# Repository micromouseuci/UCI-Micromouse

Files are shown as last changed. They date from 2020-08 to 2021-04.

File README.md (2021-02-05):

# UCI Micromouse

This is the official GitHub of Micromouse @ UCI. This repository is here to allow you to build your own mouse for competition. 

#### Club Resources
 * [__Official Club Website__](https://micromouseuci.github.io/) - Get updates on club meetings and club information
 * [__Micromouse @UCI Team Drive__](https://drive.google.com/drive/folders/1fHwfOaCsH3-F_LZoAcfiGgn9cWiebsPj) - Reference Sheets, Lecture Slides, and more informative documents
 * [__YouTube Playlist__](https://www.youtube.com/playlist?list=PLTnmBeaLzeHIIcfAZqYvjoWuxOcVnpV9Z) - Official Micromouse@UCI playlist that includes helpful video references on a wide range of subjects, ranging from soldering and safety to PID control and ChibiOS
 * [__Facebook__](https://www.facebook.com/groups/153805515376853) - Club Facebook (only UCI students can join)
 
 #### Navigation
 To help you navigate through this repository, here is an overview of each section.
 1. <strong>Schematic Reference</strong> - Shows the schematic of the PCB. Use this to refer back to the PCB as you are soldering and testing components on the PCB. 
 2. <strong>Setting Up Arduino and Teensy</strong> - How to download and set up the Arduino software and Teensy drivers
 3. <strong>Soldering Components</strong> - simple instructions on how to solder each component onto the PCB.
 4. <strong>Testing</strong> - testing components using breadboards
 5. <strong>Software</strong> - programming instructions and suggestions

 <details>
 <summary><strong>Schematic Reference</strong></summary>
 <p>This is the schematic for Micromouse at UCI's PCB. The parts are listed below the image, with the labels in parentheses. Below the labels are further explanations of each circuit so that you can get an understanding of how each circuit works and why we included them in the PCB</p>
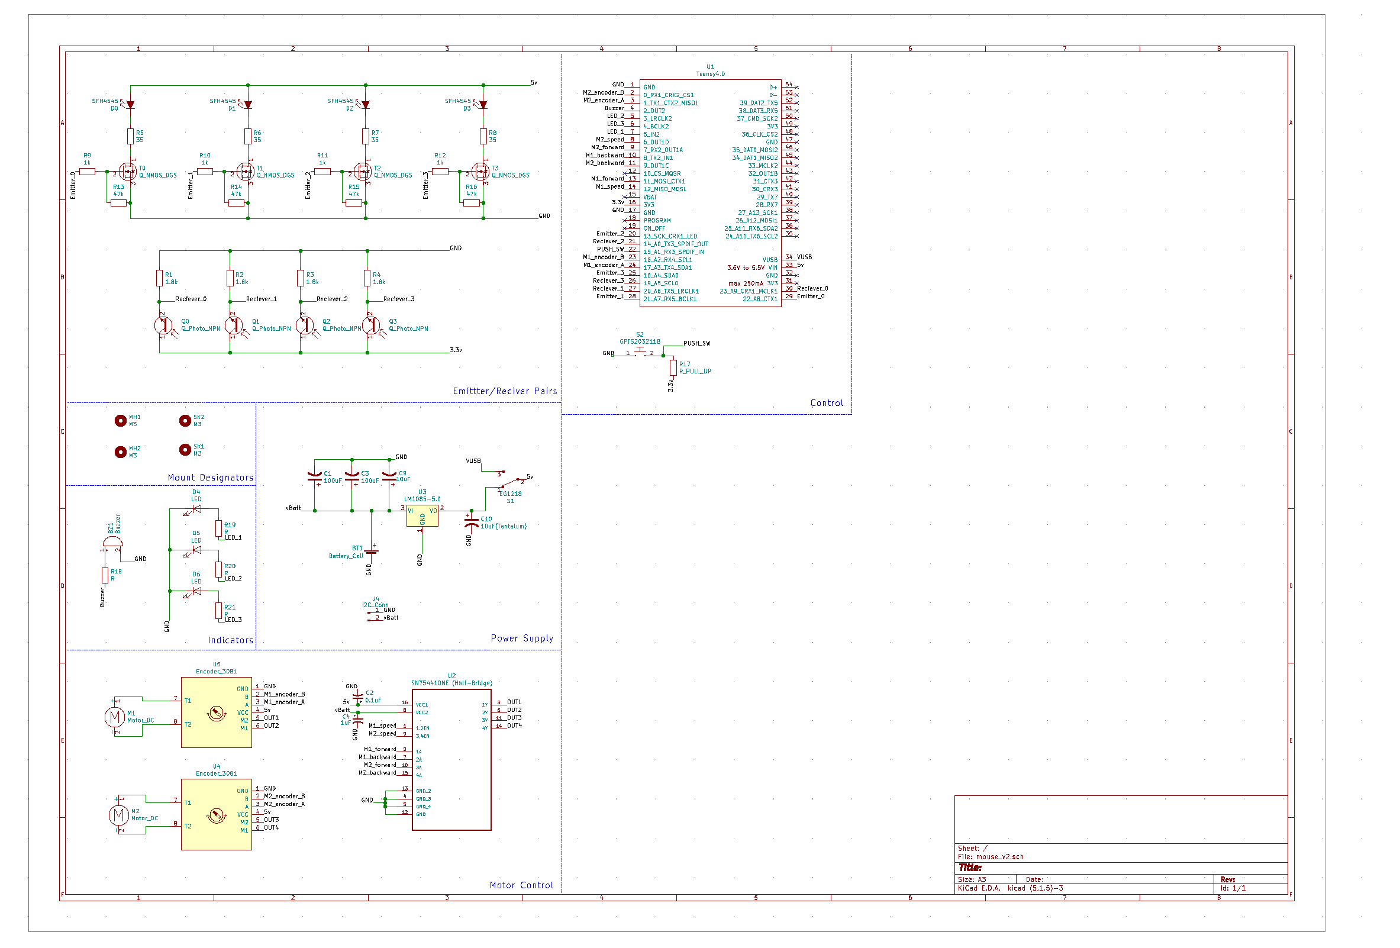
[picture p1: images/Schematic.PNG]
 
 
* [__SN754410NE__](https://www.digikey.com/product-detail/en/texas-instruments/SN754410NE/296-9911-5-ND/380180) _(U2)_ - Motor driver, used to control the speed and direction of the two motors.
* [__Teensy 3.2__](https://www.pjrc.com/teensy/teensy31.html) _(U1)_- Processor, will run code.
* [__IR Emitters__]() _(D0-D3)_ - Send an IR signal, which will bounce off walls, allowing for the reciever to read. Each is connected to a digital pin on the Teensy, allowing them to individual turn on and off.
* [__IR Reciever__]() _(Q0-Q3)_ - Reads how strong the IR signal is, depending on the value it reads it is able to detect if there is a wall, and how may cells away it is.
* [__Pololu 3081__](https://www.pololu.com/product/3081) _(U5, U4)_ - Motor encoders, used to keep track of wheel rotations.
* [__LM1085 (3A)__](http://www.ti.com/product/LM1085) _(U3)_ - Voltage regulator, a LDO regulator that gives a 5V source from the LiPo. 3A version.
* [__Switch__](http://www.google.com/search?q=mechanical+keyboard+switch) _(SW1)_ - Any mechanical keyboard switch
* [__Buzzer__](https://www.amazon.com/BETAFPV-Terminals-Electronic-Continuous-12X9-5mm/dp/B073RH8TQK) _(BZ1)_ - ~5mm buzzer pin spacing, the small ones in the link fit.
* [__LEDs__](http://www.google.com/search?q=3528+smd+led) _(D4, D5)_ - Any 3528 sized led rated for at least 3.3v
* [__Voltage Regulator (Linear)__](https://www.digikey.com/product-detail/en/stmicroelectronics/LD1085V50/497-3436-5-ND/669220) - Used to step voltage down
* __1.8KΩ__ _(R1, R2, R3, R4)_ - Current limiting resistors for Receivers.
* __35Ω__ _(R5, R6, R7, R8)_ - Current limiting resistor for Recievers.
* __47kΩ__ _(R13, R14, R15, R16)_ - Pull Up resistor for switch. Value based on the LED bought. [Calculate](http://www.ohmslawcalculator.com/led-resistor-calculator)
* __1kΩ__ _(R9, R10, R11, R12)_ - Resistors for MOSFET gate

 <details>
 <summary><strong>Emitter/Receiver Pair Circuit</strong></summary>
 </details>
 
 <details>
 <summary><strong>Power Supply Circuit</strong></summary>
 </details>

 <details>
 <summary><strong>Motor Control Circuit</strong></summary>
 </details>

 <details>
 <summary><strong>Indicator Circuit</strong></summary>
 </details>

 </details>
 
 <details>
 <summary><strong>Setting Up Arduino and Teensy</strong></summary>
 
 <p>In order to run your scripts on your computer, you will need to install Arduino.</p>
 
 * [__Download Arduino Software__]( https://www.arduino.cc/en/software) - Download the correct version based on the system you are using. Avoid downloading the Zip file if you are using Windows.
 * [__Download Teensyduino__](https://www.pjrc.com/teensy/td_download.html) - Download the Teensyduino software for your system. Make sure that you select the Teensyduino, as there are many links on this website that point to the Arduino website that you had downloaded the Arduino software from.

 </details>

<details>
 <summary><strong>Soldering Components</strong></summary>
 
 <p>The components must be soldered in order to maintain a solid electrical connection between two circuit elements. For ease, it's recommended that you follow the order listed below of components to solder. This will help prevent a mess or short circuits.</p>

   <ul><details>
 <summary><strong>Capacitors</strong></summary>
  </details></ul>

 <ul><details><summary><strong>IR Emitters and Receivers</strong></summary>
  <br> <li>On the schematic, the IR Emitters are labeled as D0, D1, D2, and D3. Find the corresponding labels on the PCB. They should be at the front of the board</li>
  <li>Place the shorter end of the emitter in the positive throughole of the corresponding pad and the longer end through the negative side. For reference, the D0 pad is shown below.</li>
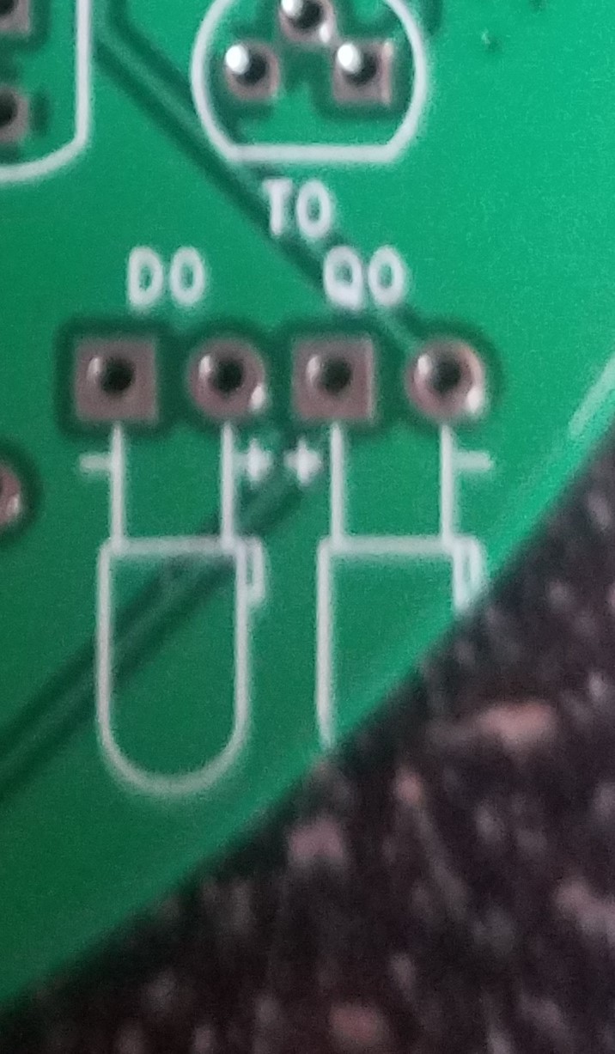
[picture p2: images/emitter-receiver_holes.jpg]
  
  <li>After inserting the emitter all the way, bend the emitter's leads so that the emitter lines up parallel to the PCB AND it is centered on the emitter sillhouette on the PCB. You can now solder the emitter. </li>
  <li>Repeat the same process for the IR Receivers. The receivers are located right next to the emitters, and are labelled as Q0, Q1, Q2, and Q3. For the receivers, the short end is also the positive end</li>
  <li>When you're soldering the components, make sure that the LEDs line up with the sillhouettes as much as possible. In other words, the length of the leads above the PCB should be as short as possible. This will ensure that one receiver from one set will not have interference from an emitter of another set. </li>
  </details></ul>
 
 <ul><details><summary><strong>Motors and Encoders</strong></summary>
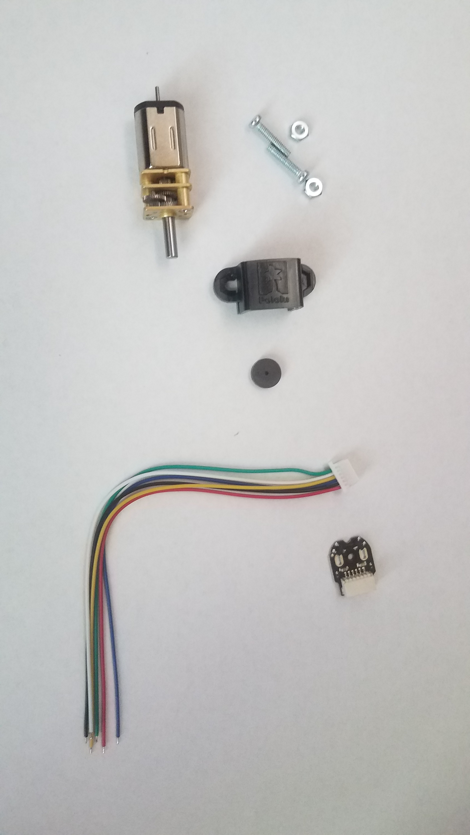
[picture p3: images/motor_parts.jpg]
 
 <ul>The image above shows all the components you will need to install your motor to your PCB.</ul>
 <ul>The first step is to attach the JST connector (the wires) to the encoder. The encoder is the mini black circuit board with a connecter pin for the JST.</ul>
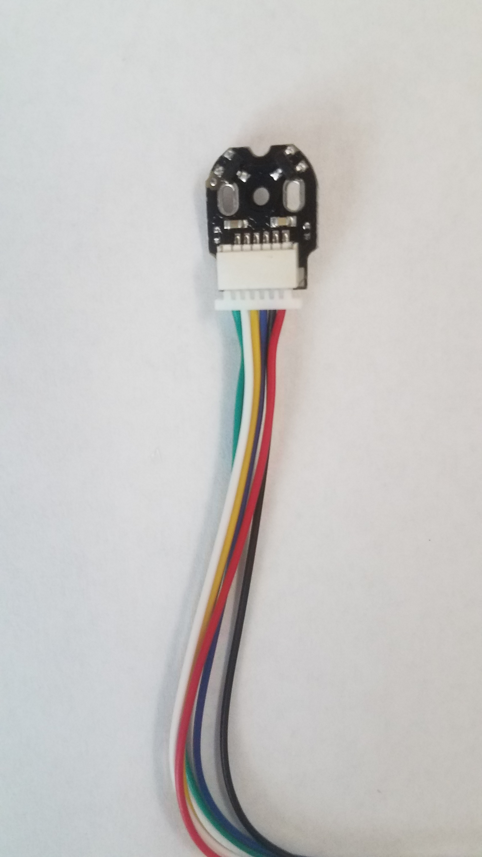
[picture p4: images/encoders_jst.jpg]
 
 <ul>To solder the encoder to the motor, use the image below as a reference. Make sure the encoder is perfectly parallel to the back end of the motor; if the encoder is crooked, it may cause some additional problems. Cover those holes on the encoder with solder while also making sure that the motor pins are touching the solder. This way, the motor pins are electrically connected to the encoders through solder. Give a slight tug to the encoder to make sure that it is firmly attached to the motor and is not loose. If it is loose, re-solder the encoder until it fits perfectly.</ul>
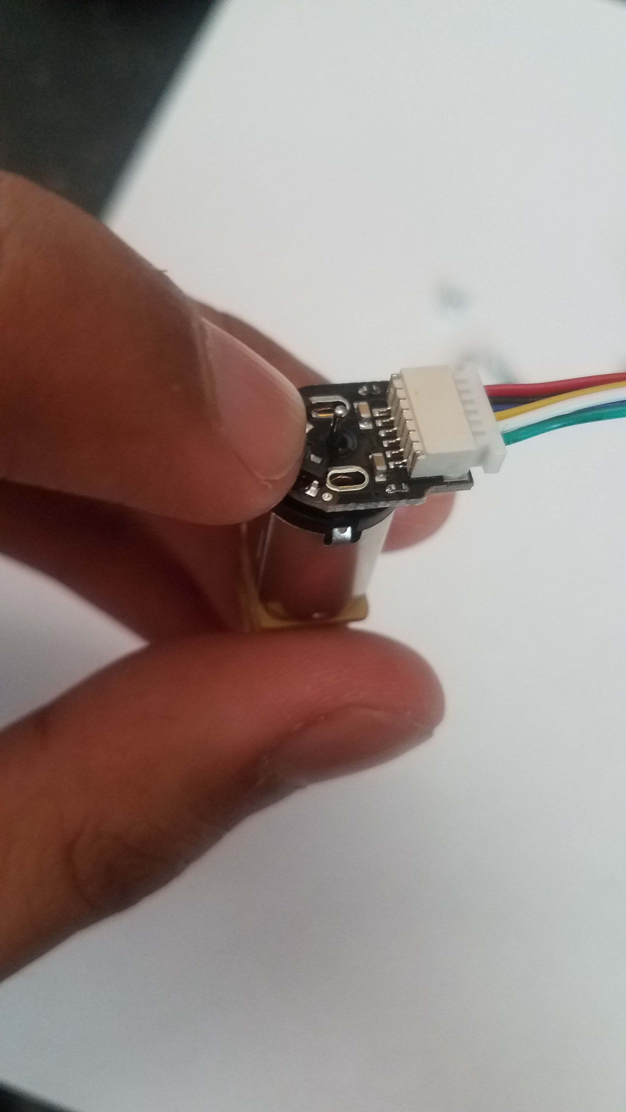
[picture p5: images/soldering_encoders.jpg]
 
 <ul>Finally, attach the magnet to the motor by inserting it through the mini shaft. The final product should look like the image below.  </ul>
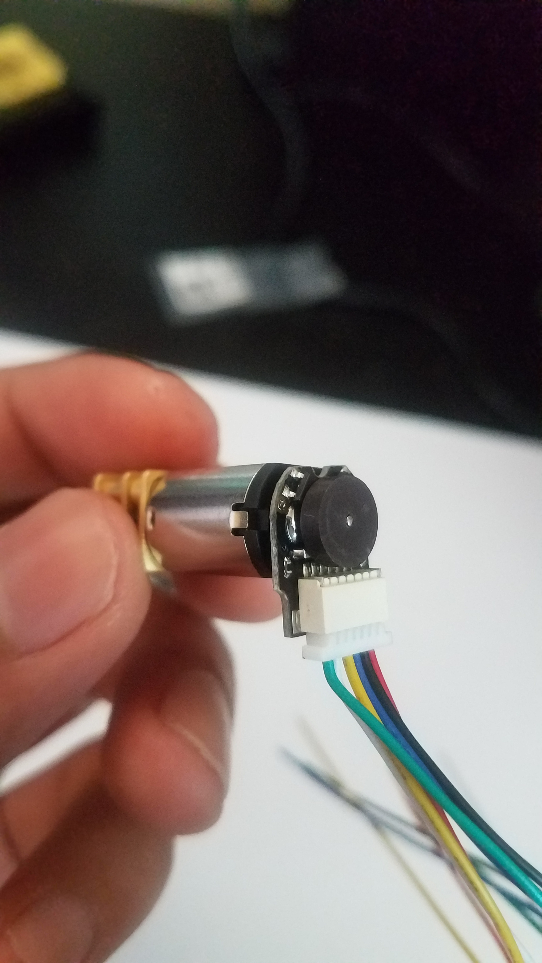
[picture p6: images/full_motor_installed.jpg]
 
 <ul> When it comes time to install the motor onto the PCB, you will need to make sure to have your motor offsets ready. First, place the motor offset onto the PCB, lining up with the motor holes. </ul>
 </details></ul>
 
 <ul><details>
 <summary><strong>MOSFETs and Resistors</strong></summary>
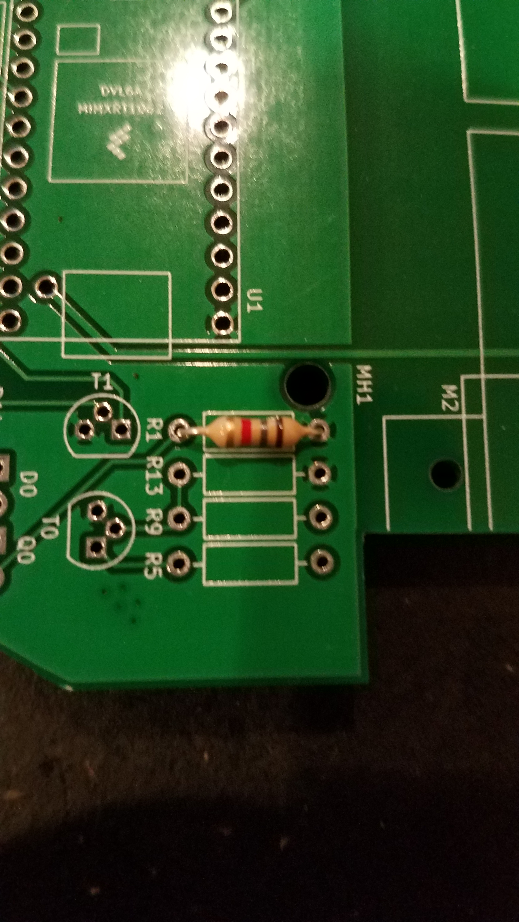
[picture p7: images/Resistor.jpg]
  
 <p>To solder the resistor, first make sure that the right resistor value is selected. Choosing the incorrect resistor value may result in irregular functionality; to determine which resistor must be used, first look at the KiCAD schematic of the mouse. Each resistor on the PCB is labeled as "R#" (i.e. R7). Find the corresponding resistor value on the schematic, and that will be the resistor value needed at that point (i.e. R7 is labeled as 35 ohms, so you will need a 35 ohm resistor at R7). To solder, simply bend the resistor and insert them into the holes specified (as shown above). The ceramic part of the resistor should be lined up with the rectangular engraving on the PCB and should touch the PCB. Solder the ends of the resistor at the bottom of the PCB, and then cut off the ends. The final product should look like this:</p>
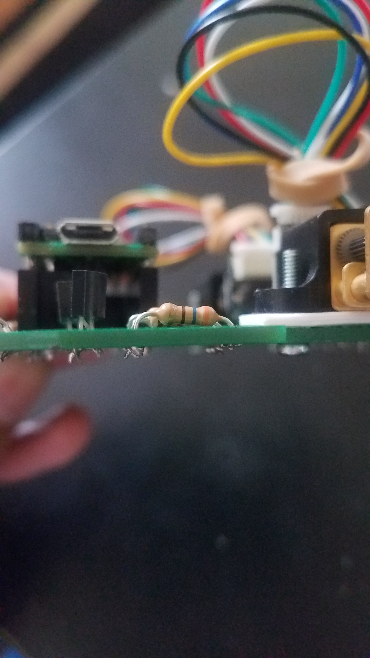
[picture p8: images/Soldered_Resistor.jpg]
 
 
 <p>The MOSFETs will be soldered on in a similar manner. All the MOSFET pads will be labeled as "T#" (i.e. T2) on the board. Place the MOSFET on the pad, with the flat face lined up with the straight edge of the MOSFET sillhouette. This will ensure the correct orientation of the transistor. Push the MOSFET in as much as you can. Solder the leads from the bottom of the board and cut off the ends. </p>
 
  </details></ul>

 <ul><details>
 <summary><strong>Voltage Regulator</strong></summary>
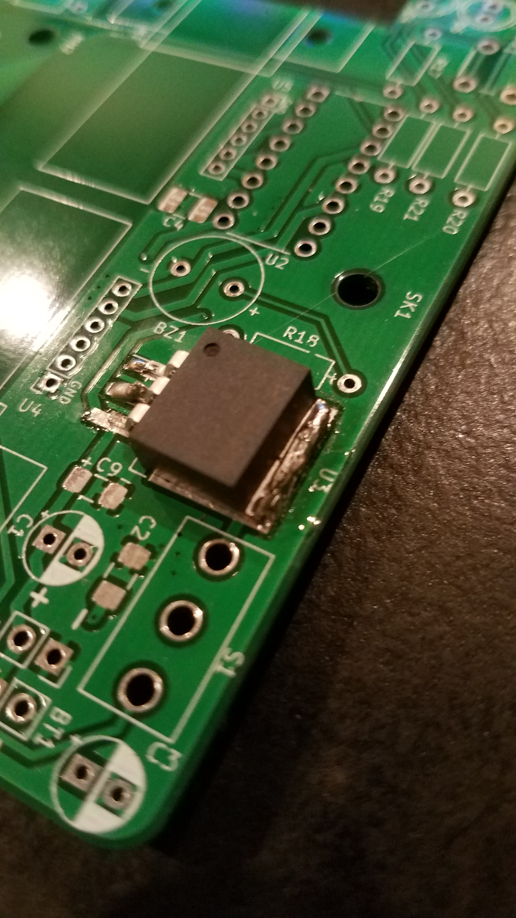
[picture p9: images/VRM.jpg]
 
 <p>YouTube Video (https://youtu.be/L_DIpklxXcI).</p>
  </details></ul> 

   <ul><details>
 <summary><strong>Switches and Buzzer</strong></summary>
  </details></ul>
  
   <ul><details>
 <summary><strong>Header Pins & Dip Socket</strong></summary>
 <ul>The header pins and dip socket are used for easy replacement of the Teensy and motor driver respectively in the event that they burn out. </ul>
 <ul>For the Teensy, you will need two 1x14 headers and one 1x5 header. Solder them on individually in the location shown below</ul>
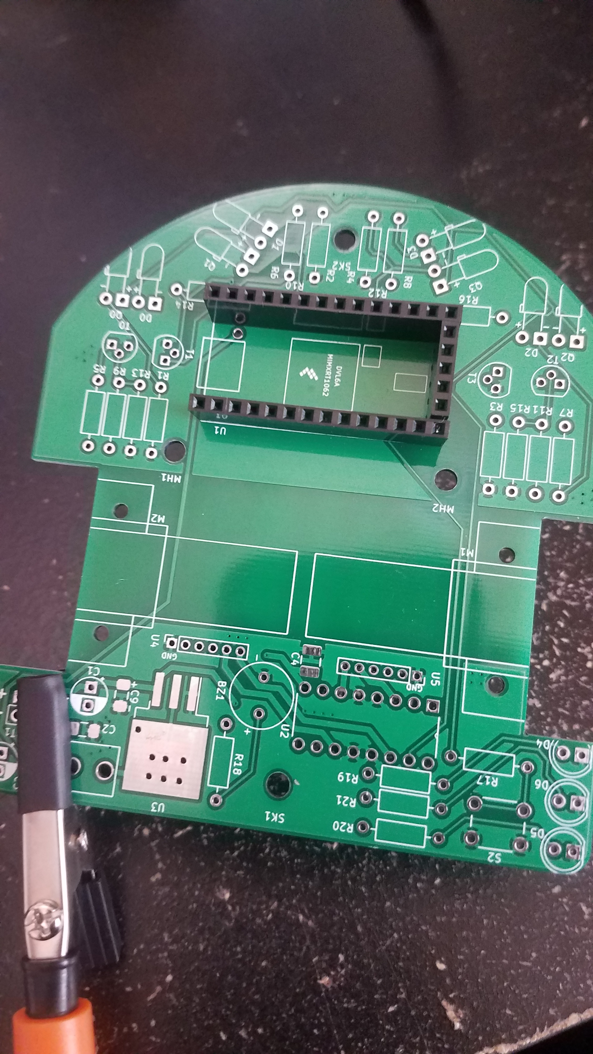
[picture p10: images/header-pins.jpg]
 
  
  </details></ul>
  <ul><details>
  <summary><strong>Header Pins for Teensy</strong></summary>
 <p>To add connections to the Teensy, male header pins must be installed onto the Teensy. Open the pack of male header pins, and break off two pieces of 14-unit pins (since the Teensy has 14 pins lengthwise) and one 5-unit piece (widthwise). When soldering the pins on, ensure that the black caps go UNDER the Teensy board, and not on top (image shown below). Once you solder them, cut off the top leads. You will also need to insert 1 pin into the final hole in the Teensy. You should now be able to place the Teensy on the header pins.  </p>
 
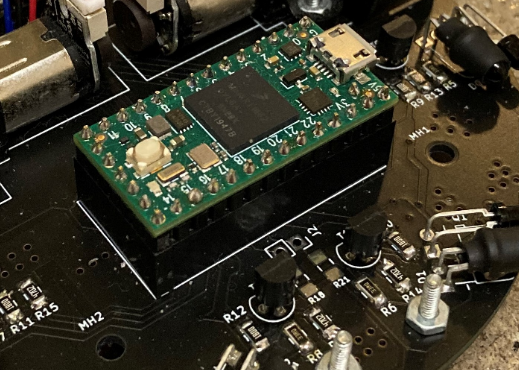
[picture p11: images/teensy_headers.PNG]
 
 
  </details></ul>
 
</details>
 
<details>
<summary><strong>Testing</strong></summary>
 
 <ul><details><summary><strong>IR Sensors</strong></summary>

</details></ul>

<ul><details>
<summary><strong>Motors</strong></summary>

</details></ul>

</details>
 
<details>
<summary><strong>Software</strong></summary>

#### Interrupts

* Interrupts are needed to keep track of the wheels revolution. When the wheels position changes, the motor encoder will send a signal to the Teensy. A total of 12 signals will be sent per 1 revolution. Interrupts allow it so the Teensy can update values as soon as the encoder sends the signal (asynchronously). If the encoders were updated in the main loop theres a good chance for some signals to be missed, causing the revolution count to be inaccurate.   

* To add an interrupt run the [attatchInterrupt](https://www.arduino.cc/reference/en/language/functions/external-interrupts/attachinterrupt/) function in setup. Syntax is **attatchInterrupt(pin, func, mode)**. The second parameter specifies the function that gets executed when the interrupt is triggered. In our case we want to put in a function that will add to the count of an encoder variable. The third parameter specifies what will trigger the interrupt. For example "CHANGE" will make the interrupt trigger whenever the pin changes value, however, "FALLING" will make the interrupt trigger only when the pin goes from HIGH to LOW. Read link for more info.

#### Variables

* tickCount - Two variables, one for each motor. When interrupt its triggered, increment the tick count by 1.
* emitterState - One for each emitter. Stores the current state of the emitter

#### Functions

* readReciever() - One method for each reciever. Returns the value read by reciever
* setEmitterState(x) - One method for each emitter. Set the state of the emitter to on or off.
* getSwitchState() - Return the value of the switch
* runMotorTime(m, speed, sec) - Set specific motor at speed for given amount of seconds. Uses delay function to count time.
* runMotorRev(m, speed, rev) - Runs a specific motor at speed for given amount of revolutions. Uses the encoder varible to count revolutions.
* setLED(l, brightness) - Sets a specific led to a certian brightness.
* setBuzzer(strength) - Sets the buzzer to a given strength.

#### More Functions
* turnRight() - Use encoders and tickCounts of both motors to make a percise right turn
* turnLeft() - similar to turnRight()
* goForward() - Use encoders to go straight.
* turnAround() - turnRight * 2

 </details>
 
 <details>
<summary><strong>3D Printed Parts</strong></summary>
 </details>

### Other Resources

<li><a href="https://git-scm.com/book/en/v2" target="_blank"><strong>Git Markdown</strong></a></li>
<li><a href="https://www.sparkfun.com/tutorials/223" target="_blank"><strong>How to Read a Datasheet</strong></a></li>

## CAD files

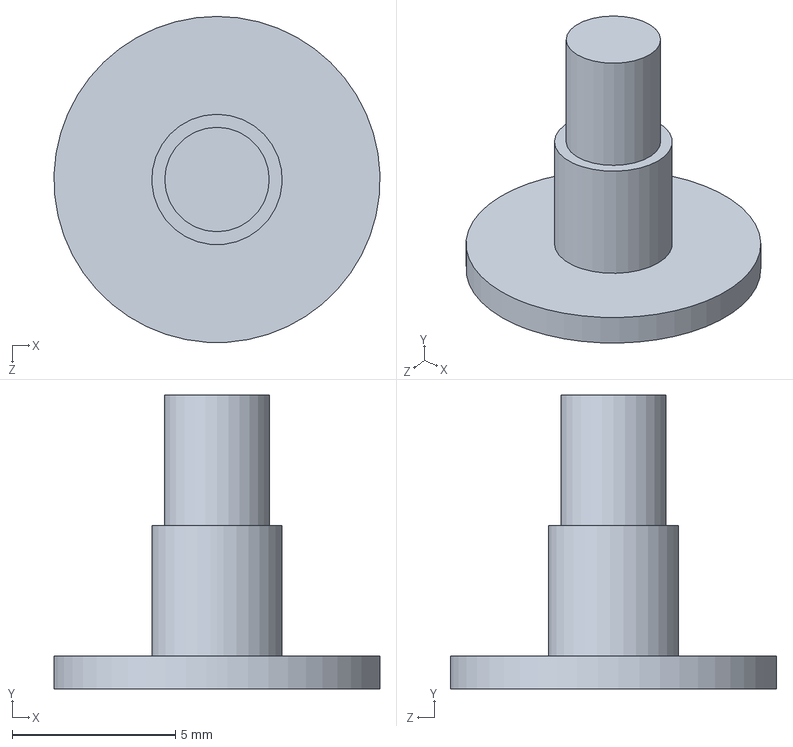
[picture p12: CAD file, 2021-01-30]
CAD Files/flat skates.SLDPRT
9.99 x 9.00 x 10.0 mm

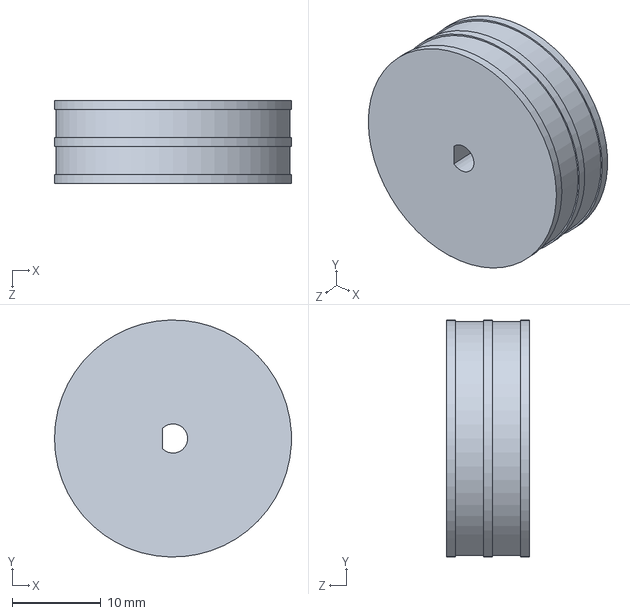
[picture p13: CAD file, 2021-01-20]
CAD Files/27 Rubber Band Wheel.SLDPRT
26.8 x 26.7 x 9.35 mm

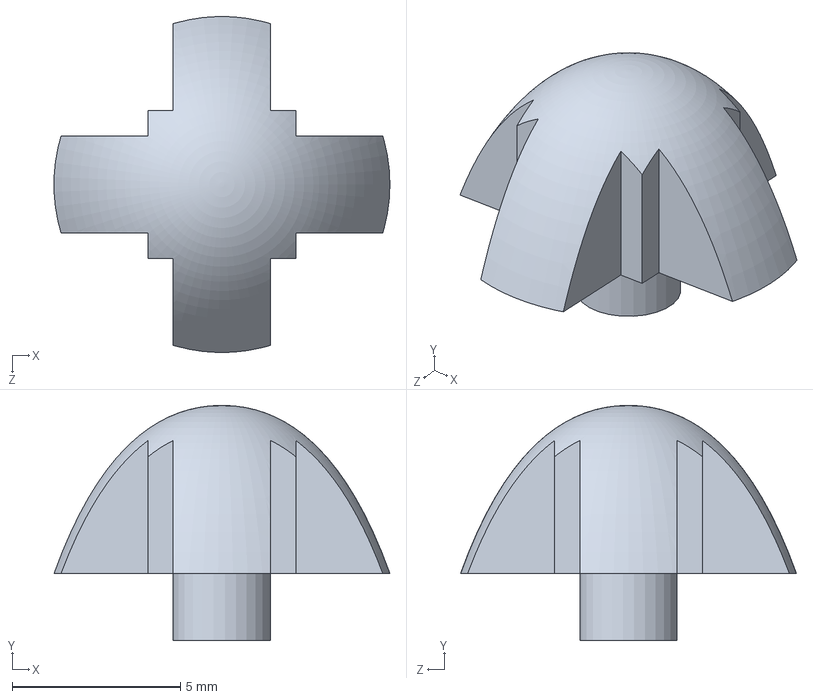
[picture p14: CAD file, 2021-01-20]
CAD Files/Mouse Skates.SLDPRT
10.00 x 7.00 x 10.00 mm

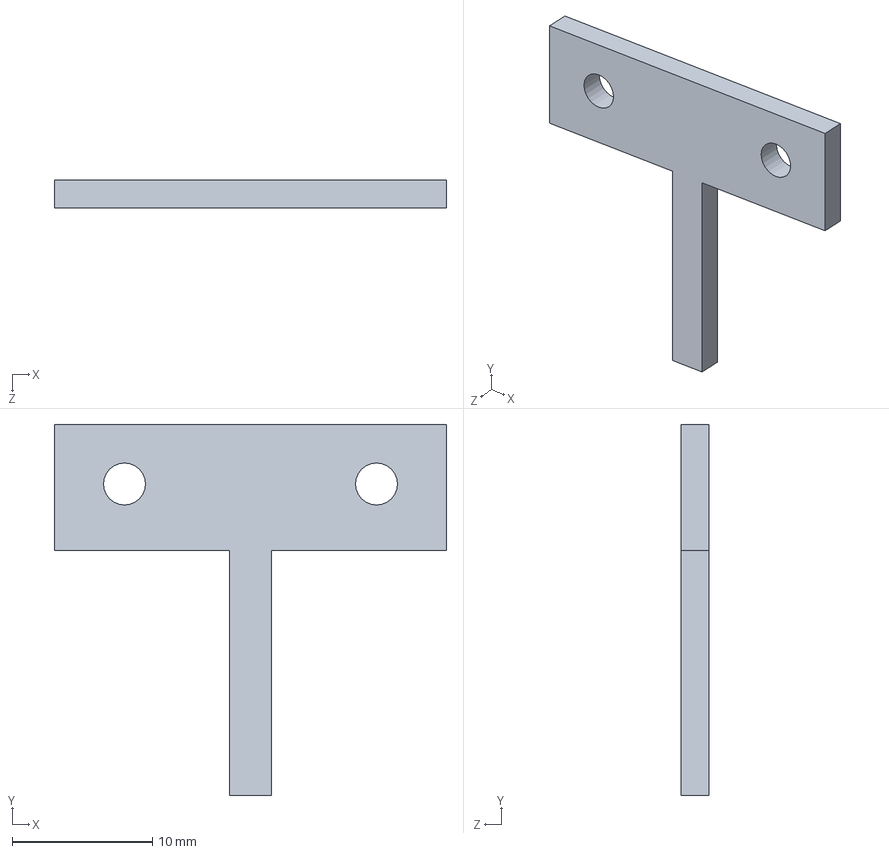
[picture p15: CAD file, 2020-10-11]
CAD Files/Motor Offset.SLDPRT
28.0 x 26.5 x 2.00 mm

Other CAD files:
CAD Files/27 Rubber Band Wheel.STL
CAD Files/Mouse Skates.STL
CAD Files/flat skates.STL

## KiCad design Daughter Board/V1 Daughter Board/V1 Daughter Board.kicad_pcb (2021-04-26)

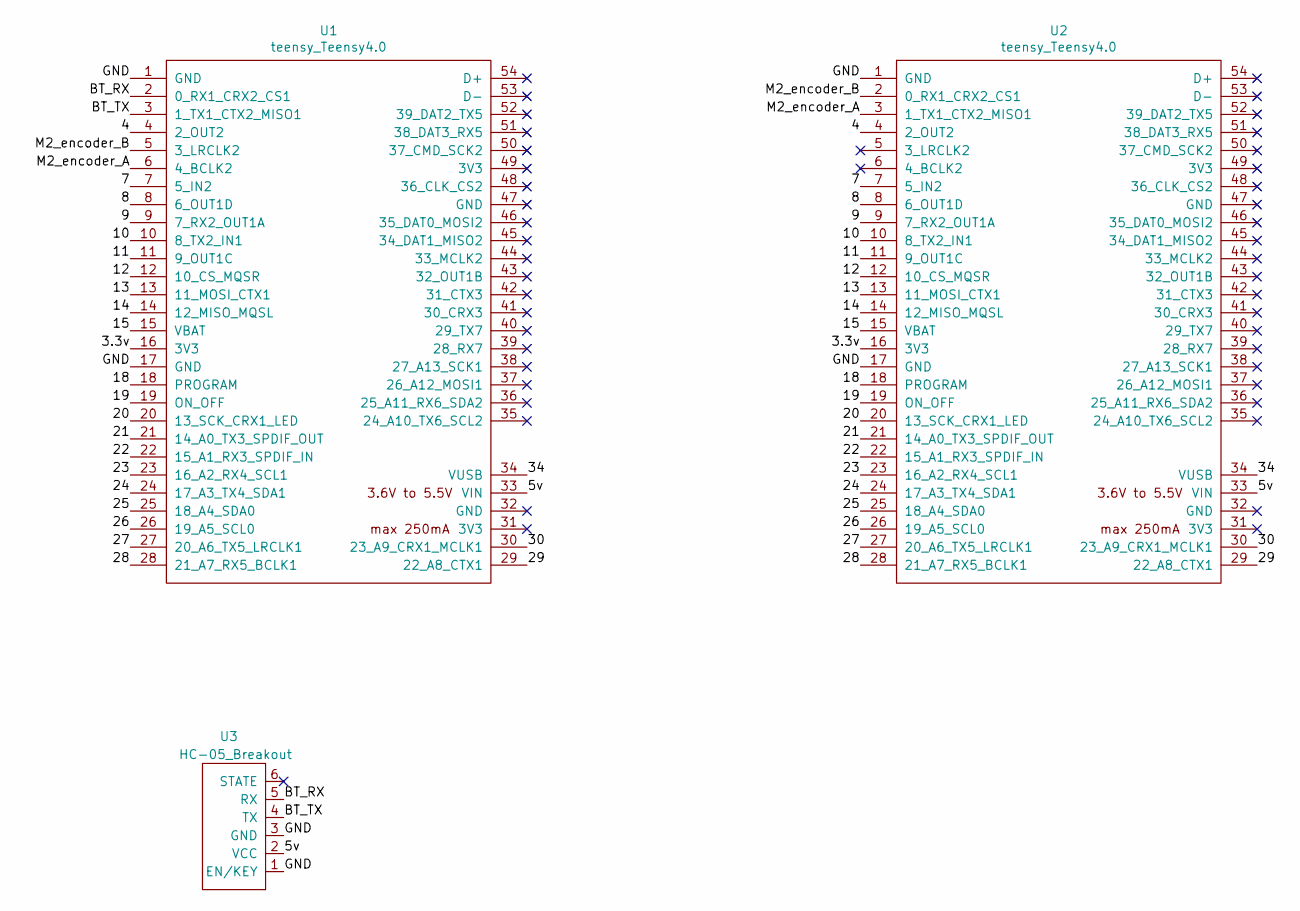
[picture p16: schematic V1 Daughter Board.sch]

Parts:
U1, U2: teensy_Teensy4.0; Teensy40_nosmd
U3: HC-05_Breakout

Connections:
/3.3v: U1.16 (3V3), U2.16 (3V3)
/4: U1.4 (2_OUT2), U2.4 (2_OUT2)
/5v: U1.33 (VIN), U2.33 (VIN), U3.2 (VCC)
/7: U1.7 (5_IN2), U2.7 (5_IN2)
/8: U1.8 (6_OUT1D), U2.8 (6_OUT1D)
/9: U1.9 (7_RX2_OUT1A), U2.9 (7_RX2_OUT1A)
/10: U1.10 (8_TX2_IN1), U2.10 (8_TX2_IN1)
/11: U1.11 (9_OUT1C), U2.11 (9_OUT1C)
/12: U1.12 (10_CS_MQSR), U2.12 (10_CS_MQSR)
/13: U1.13 (11_MOSI_CTX1), U2.13 (11_MOSI_CTX1)
/14: U1.14 (12_MISO_MQSL), U2.14 (12_MISO_MQSL)
/15: U1.15 (VBAT), U2.15 (VBAT)
/18: U1.18 (PROGRAM), U2.18 (PROGRAM)
/19: U1.19 (ON_OFF), U2.19 (ON_OFF)
/20: U1.20 (13_SCK_CRX1_LED), U2.20 (13_SCK_CRX1_LED)
/21: U1.21 (14_A0_TX3_SPDIF_OUT), U2.21 (14_A0_TX3_SPDIF_OUT)
/22: U1.22 (15_A1_RX3_SPDIF_IN), U2.22 (15_A1_RX3_SPDIF_IN)
/23: U1.23 (16_A2_RX4_SCL1), U2.23 (16_A2_RX4_SCL1)
/24: U1.24 (17_A3_TX4_SDA1), U2.24 (17_A3_TX4_SDA1)
/25: U1.25 (18_A4_SDA0), U2.25 (18_A4_SDA0)
/26: U1.26 (19_A5_SCL0), U2.26 (19_A5_SCL0)
/27: U1.27 (20_A6_TX5_LRCLK1), U2.27 (20_A6_TX5_LRCLK1)
/28: U1.28 (21_A7_RX5_BCLK1), U2.28 (21_A7_RX5_BCLK1)
/29: U1.29 (22_A8_CTX1), U2.29 (22_A8_CTX1)
/30: U1.30 (23_A9_CRX1_MCLK1), U2.30 (23_A9_CRX1_MCLK1)
/34: U1.34 (VUSB), U2.34 (VUSB)
/BT_RX: U1.2 (0_RX1_CRX2_CS1), U3.5 (RX)
/BT_TX: U1.3 (1_TX1_CTX2_MISO1), U3.4 (TX)
/GND: U1.1 (GND), U1.17 (GND), U2.1 (GND), U2.17 (GND), U3.1 (EN/KEY), U3.3 (GND)
/M2_encoder_A: U1.6 (4_BCLK2), U2.3 (1_TX1_CTX2_MISO1)
/M2_encoder_B: U1.5 (3_LRCLK2), U2.2 (0_RX1_CRX2_CS1)

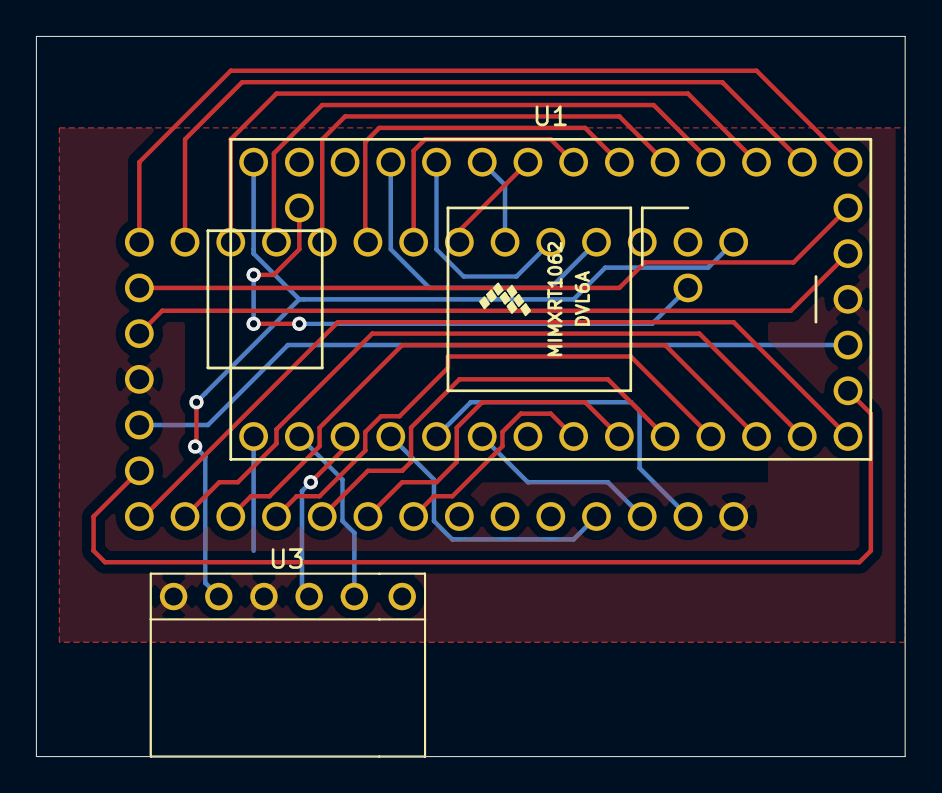
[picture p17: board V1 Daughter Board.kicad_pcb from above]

Board: 2 copper layers, 48.3 x 40.0 mm, 3 parts (1 on the bottom side), 31 nets.

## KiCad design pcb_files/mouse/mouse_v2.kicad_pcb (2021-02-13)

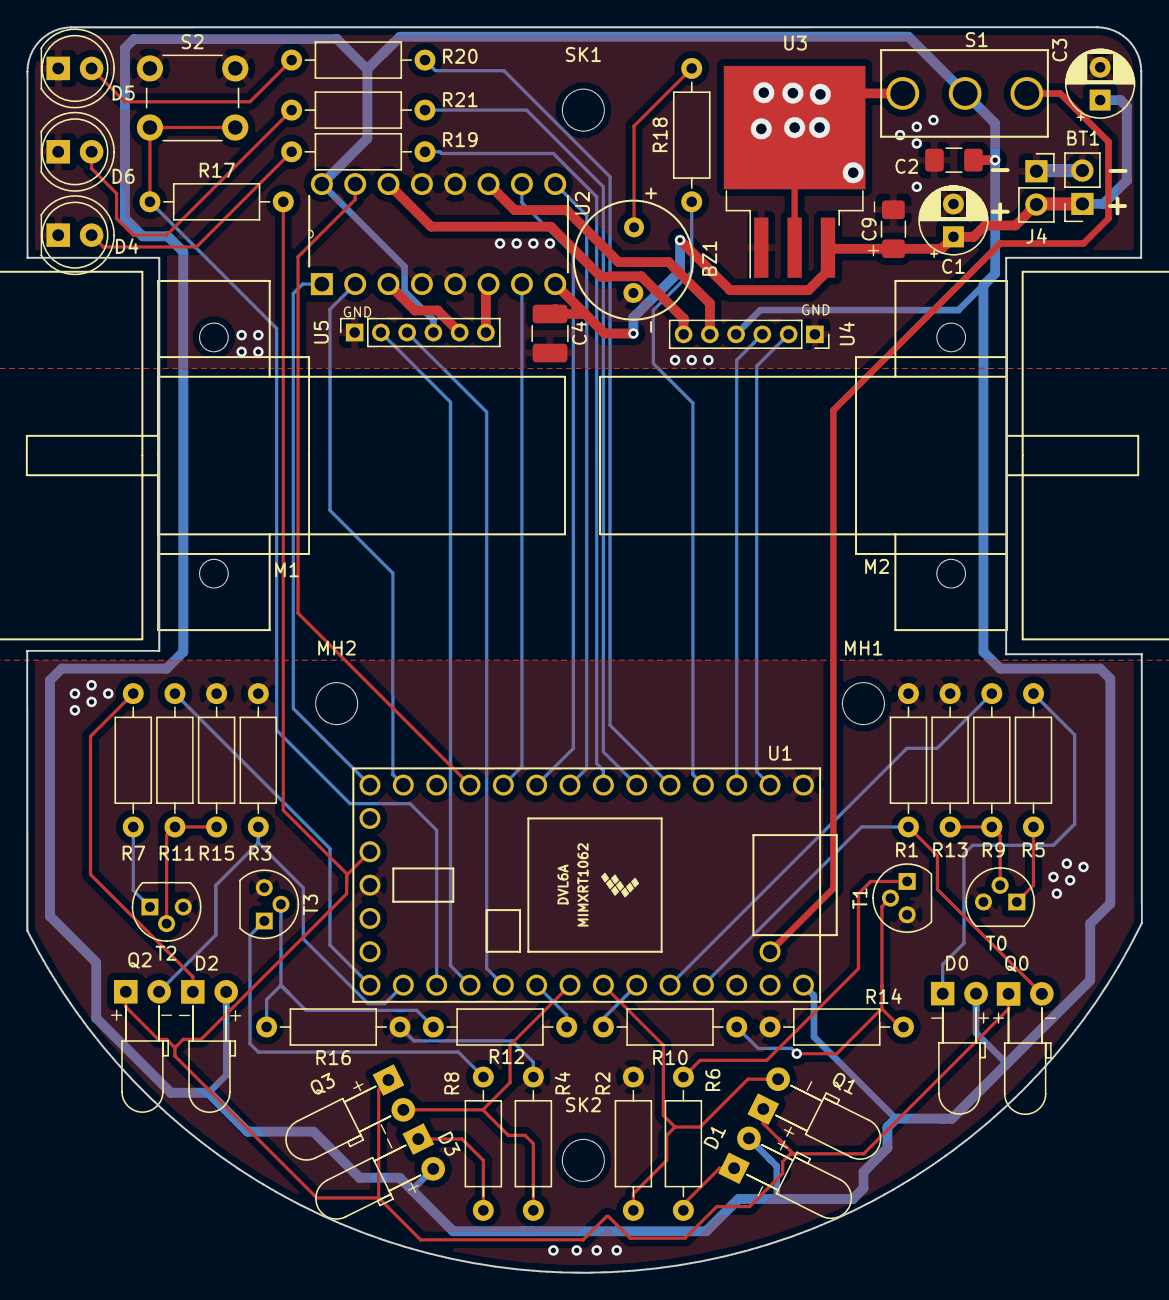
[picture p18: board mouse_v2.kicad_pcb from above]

Board: 2 copper layers, 84.9 x 94.9 mm, 58 parts (1 on the bottom side), 49 nets.

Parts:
BT1: Battery_Cell; PinSocket_1x02_P2.54mm_Vertical
BZ1: Buzzer; 9x5.5mm Buzzer
C1, C3: 100uF; CP_Radial_D5.0mm_P2.50mm
C2: 0.1uF; C_1206_3216Metric_Pad1.42x1.75mm_HandSolder
C4: 1uF; C_1210_3225Metric_Pad1.42x2.65mm_HandSolder
C9: 10uF; C_1206_3216Metric_Pad1.42x1.75mm_HandSolder
C10: 10uF(Tantalum); C_1206_3216Metric_Pad1.42x1.75mm_HandSolder
D0, D1, D2, D3: SFH4545; LED_D3.0mm_Horizontal_O3.81mm_Z2.0mm
D4, D5, D6: LED; LED_D5.0mm
J4: I2C_Conn; PinSocket_1x02_P2.54mm_Vertical
M1, M2: Motor_DC; Motor_mouse
MH1, MH2: M3; MountingHole_3.2mm_M3
Q0, Q1, Q2, Q3: Q_Photo_NPN; LED_D3.0mm_Horizontal_O3.81mm_Z2.0mm
R1, R2, R3, R4: 1.8k; R_Axial_DIN0207_L6.3mm_D2.5mm_P10.16mm_Horizontal
R5, R6, R7, R8: 35; R_Axial_DIN0207_L6.3mm_D2.5mm_P10.16mm_Horizontal
R9, R10, R11, R12: 1k; R_Axial_DIN0207_L6.3mm_D2.5mm_P10.16mm_Horizontal
R13, R14, R15, R16: 47k; R_Axial_DIN0207_L6.3mm_D2.5mm_P10.16mm_Horizontal
R17: R_PULL_UP; R_Axial_DIN0207_L6.3mm_D2.5mm_P10.16mm_Horizontal
R18, R19, R20, R21: R; R_Axial_DIN0207_L6.3mm_D2.5mm_P10.16mm_Horizontal
S1: EG1218; SWITCH_SLIDE_500SSP1S2M2QEA
S2: GPTS203211B; SW_PUSH_6mm
SK1, SK2: M3; MountingHole_3.2mm_M3
T0, T1, T2, T3: Q_NMOS_DGS; TN0104(TO-92)v2
U1: Teensy4.0; Teensy40(nopads)
U2: SN754410NE (Half-Bridge); DIP254P762X508-16
U3: LM1085-5.0; TO-263-3_TabPin2
U4, U5: Encoder_3081; PinSocket_1x06_P2.00mm_Vertical

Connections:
/3.3v: Q0.1, Q1.1, Q2.1, Q3.1, R17.2, U1.16
/5v: C2.1, D0.2, D1.2, D2.2, D3.2, S1.2, U1.33, U2.16, U4.4, U5.4
/Buzzer: R18.1, U1.4
/Emitter_0: R9.2, U1.29
/Emitter_1: R10.2, U1.28
/Emitter_2: R11.2, U1.20
/Emitter_3: R12.2, U1.25
/GND: BT1.2, BZ1.2, C1.2, C2.2, C3.2, C4.2, C9.2, C10.2, D4.1, D5.1, D6.1, J4.1, R1.1, R2.1, R3.1, R4.1, R13.1, R14.1, R15.1, R16.1, S2.1, T0.3, T1.3, T2.3, T3.3, U1.1, U1.17, U2.4, U2.5, U2.12, U2.13, U3.1, U4.1, U5.1
/LED_1: R19.2, U1.7
/LED_2: R20.2, U1.5
/LED_3: R21.2, U1.6
/M1_backward: U1.10, U2.7
/M1_encoder_A: U1.24, U5.3
/M1_encoder_B: U1.23, U5.2
/M1_forward: U1.13, U2.2
/M1_speed: U1.14, U2.1
/M2_backward: U1.11, U2.15
/M2_encoder_A: U1.3, U4.3
/M2_encoder_B: U1.2, U4.2
/M2_forward: U1.9, U2.10
/M2_speed: U1.8, U2.9
/OUT1: U2.3, U5.5
/OUT2: U2.6, U5.6
/OUT3: U2.11, U4.5
/OUT4: U2.14, U4.6
/PUSH_SW: R17.1, S2.2, U1.22
/Reciever_0: Q0.2, R1.2, U1.30
/Reciever_1: Q1.2, R2.2, U1.27
/Reciever_2: Q2.2, R3.2, U1.21
/Reciever_3: Q3.2, R4.2, U1.26
/VUSB: S1.3, U1.34
/vBatt: BT1.1, C1.1, C3.1, C4.1, C9.1, J4.2, U2.8, U3.3
unnamed: BZ1.1, R18.2
unnamed: C10.1, S1.1, U3.2
unnamed: D0.1, R5.1
unnamed: D1.1, R6.1
unnamed: D2.1, R7.1
unnamed: D3.1, R8.1
unnamed: D4.2, R19.1
unnamed: D5.2, R20.1
unnamed: D6.2, R21.1
unnamed: R5.2, T0.1
unnamed: R6.2, T1.1
unnamed: R7.2, T2.1
unnamed: R8.2, T3.1
unnamed: R10.1, R14.2, T1.2
unnamed: R11.1, R15.2, T2.2
unnamed: R12.1, R16.2, T3.2
unnamed: R9.1, R13.2, T0.2

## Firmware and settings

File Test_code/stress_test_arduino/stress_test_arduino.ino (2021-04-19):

#define EMITTER_ON_TIME 2

#define EMIT_L_PIN 21 //D1
#define EMIT_R_PIN 18//D3
#define EMIT_FL_PIN 22 //D0
#define EMIT_FR_PIN 13 //D2

#define RECIVER_L_PIN 20 //Q1
#define RECIVER_R_PIN 19 //Q3
#define RECIVER_FL_PIN 23 //Q0
#define RECIVER_FR_PIN 14 //Q2

#define M1_BACK_PIN 8
#define M1_FWD_PIN 11
#define M1_SPD_PIN 12
#define M1_ENC_A_PIN 17
#define M1_ENC_B_PIN 16

#define M2_BACK_PIN 9
#define M2_FWD_PIN 7
#define M2_SPD_PIN 6
#define M2_ENC_A_PIN 1
#define M2_ENC_B_PIN 0

unsigned int enc_a_l_count = 0;
unsigned int enc_b_l_count = 0;
unsigned int enc_a_r_count = 0;
unsigned int enc_b_r_count = 0;

#define BUZZ_PIN 2
#define SW_1_PIN 15
#define LED1_PIN 5
#define LED2_PIN 3
#define LED3_PIN 4
//#define SW_2_PIN 12
//#define RGB_DATA_PIN 10

enum Direction {
  FORWARDS = 0, BACKWARDS = 1, STOP = 2
};

void enc_a_l_intr_handler() {
  enc_a_l_count++;
  Serial.print("ENCAL: ");
  Serial.println(enc_a_l_count);
}

void enc_b_l_intr_handler() {
  enc_b_l_count++;
  Serial.print("ENCbL: ");
  Serial.println(enc_b_l_count);
}

void enc_a_r_intr_handler() {
  enc_a_r_count++;
  Serial.print("ENCAR: ");
  Serial.println(enc_a_r_count);
}

void enc_b_r_intr_handler() {
  enc_b_r_count++;
  Serial.print("ENCBR: ");
  Serial.println(enc_b_r_count);
}


void setup() {
  Serial.begin(9600);
  pinMode(EMIT_L_PIN, OUTPUT);
  pinMode(EMIT_R_PIN, OUTPUT);
  pinMode(EMIT_FL_PIN, OUTPUT);
  pinMode(EMIT_FR_PIN, OUTPUT);

  pinMode(RECIVER_L_PIN, INPUT);
  pinMode(RECIVER_R_PIN, INPUT);
  pinMode(RECIVER_FL_PIN, INPUT);
  pinMode(RECIVER_FR_PIN, INPUT);

  pinMode(M1_BACK_PIN, OUTPUT);
  pinMode(M1_FWD_PIN, OUTPUT);
  pinMode(M1_SPD_PIN, OUTPUT);
  pinMode(M1_ENC_A_PIN, INPUT); //check if input pullup
  pinMode(M1_ENC_B_PIN, INPUT);

  pinMode(M2_BACK_PIN, OUTPUT);
  pinMode(M2_FWD_PIN, OUTPUT);
  pinMode(M2_SPD_PIN, OUTPUT);
  pinMode(M2_ENC_A_PIN, INPUT); //check if input pullup
  pinMode(M2_ENC_B_PIN, INPUT);

  pinMode(BUZZ_PIN, OUTPUT);
  pinMode(SW_1_PIN, INPUT);
  //pinMode(RGB_DATA_PIN, OUTPUT);

  analogWriteFrequency(M1_BACK_PIN, 488.28);
  analogWriteFrequency(M1_FWD_PIN, 488.28);
  analogWriteFrequency(M1_SPD_PIN, 488.28);
  analogWriteFrequency(M2_BACK_PIN, 488.28);
  analogWriteFrequency(M2_FWD_PIN, 488.28);
  analogWriteFrequency(M2_SPD_PIN, 488.28);
  
  analogWriteFrequency(BUZZ_PIN, 488.28);

  //Interrupts
  attachInterrupt(M2_ENC_A_PIN, enc_a_l_intr_handler, FALLING); //check if rising or falling
  attachInterrupt(M2_ENC_B_PIN, enc_b_l_intr_handler, FALLING);
  attachInterrupt(M1_ENC_A_PIN, enc_a_r_intr_handler, FALLING);
  attachInterrupt(M1_ENC_B_PIN, enc_b_r_intr_handler, FALLING);
  delay(2000);
}


//implement data averaging ??
int get_dist_l() {
  int dist;
  digitalWrite(EMIT_L_PIN, HIGH);
  delay(EMITTER_ON_TIME);
  dist = analogRead(RECIVER_L_PIN);
  digitalWrite(EMIT_L_PIN, LOW);
  return dist;
}

int get_dist_r() {
  int dist;
  digitalWrite(EMIT_R_PIN, HIGH);
  delay(EMITTER_ON_TIME);
  dist = analogRead(RECIVER_R_PIN);
  digitalWrite(EMIT_R_PIN, LOW);
  return dist;
}

int get_dist_fr() {
  int dist;
  digitalWrite(EMIT_FR_PIN, HIGH);
  delay(EMITTER_ON_TIME);
  dist = analogRead(RECIVER_FR_PIN);
  digitalWrite(EMIT_FR_PIN, LOW);
  return dist;
}

int get_dist_fl() {
  int dist;
  digitalWrite(EMIT_FL_PIN, HIGH);
  delay(EMITTER_ON_TIME);
  dist = analogRead(RECIVER_FL_PIN);
  digitalWrite(EMIT_FL_PIN, LOW);
  return dist;
}

void turn_all_emit_on(){
  digitalWrite(EMIT_FL_PIN, HIGH);
  digitalWrite(EMIT_FR_PIN, HIGH);
  digitalWrite(EMIT_R_PIN, HIGH);
  digitalWrite(EMIT_L_PIN, HIGH);
}

void turn_all_emit_off(){
  digitalWrite(EMIT_FL_PIN, LOW);
  digitalWrite(EMIT_FR_PIN, LOW);
  digitalWrite(EMIT_R_PIN, LOW);
  digitalWrite(EMIT_L_PIN, LOW);
}

void turn_all_led_on(){
  digitalWrite(LED1_PIN, HIGH);
  digitalWrite(LED2_PIN, HIGH);
  digitalWrite(LED3_PIN, HIGH);
}


void turn_all_led_off(){
  digitalWrite(LED1_PIN, LOW);
  digitalWrite(LED2_PIN, LOW);
  digitalWrite(LED3_PIN, LOW);
}


void set_motor_l(int dir, int mspeed) {
  if (dir == 0) {
    digitalWrite(M2_FWD_PIN, LOW);
    digitalWrite(M2_BACK_PIN, HIGH);
    analogWrite(M2_SPD_PIN, mspeed);
  }
  else if (dir == 1) {
    digitalWrite(M2_FWD_PIN, HIGH);
    digitalWrite(M2_BACK_PIN, LOW);
    analogWrite(M2_SPD_PIN, mspeed);
  }
  else if (dir == 2) {
    digitalWrite(M2_FWD_PIN, LOW);
    digitalWrite(M2_BACK_PIN, LOW);
    analogWrite(M2_SPD_PIN, 0);
  }
  else {
    //incorrect direction given
  }
}

void set_motor_r(int dir, int mspeed) {
  if (dir == 0) {

    digitalWrite(M1_BACK_PIN, LOW);
    digitalWrite(M1_FWD_PIN, HIGH);
    analogWrite(M1_SPD_PIN, mspeed);
  }
  else if (dir == 1) {
    digitalWrite(M1_FWD_PIN, LOW);
    digitalWrite(M1_BACK_PIN, HIGH);
    analogWrite(M1_SPD_PIN, mspeed);
  }
  else if (dir == 2) {
    analogWrite(M1_SPD_PIN, 0);
    digitalWrite(M1_FWD_PIN, LOW);
    digitalWrite(M1_BACK_PIN, LOW);

  }
  else {
    //incorrect direction given
  }
}

void set_motor_l_pulse_dir(int dir, int mspeed) {
  if (dir == 0) {
    digitalWrite(M2_FWD_PIN, LOW);
    digitalWrite(M2_SPD_PIN, HIGH);
    analogWrite(M2_BACK_PIN, mspeed);
  }
  else if (dir == 1) {
    digitalWrite(M2_BACK_PIN, LOW);
    digitalWrite(M2_SPD_PIN, HIGH);
    analogWrite(M2_FWD_PIN, mspeed);
  }
  else if (dir == 2) {
    digitalWrite(M2_FWD_PIN, LOW);
    digitalWrite(M2_BACK_PIN, LOW);
    analogWrite(M2_SPD_PIN, 0);
  }
  else {
    //incorrect direction given
  }
}

void set_motor_r_pulse_dir(int dir, int mspeed) {
  if (dir == 0) {

    digitalWrite(M1_BACK_PIN, LOW);
    digitalWrite(M1_SPD_PIN, HIGH);
    analogWrite(M1_FWD_PIN, mspeed);
  }
  else if (dir == 1) {
    digitalWrite(M1_FWD_PIN, LOW);
    digitalWrite(M1_SPD_PIN, HIGH);
    analogWrite(M1_BACK_PIN, mspeed);
  }
  else if (dir == 2) {
    analogWrite(M1_SPD_PIN, 0);
    digitalWrite(M1_FWD_PIN, LOW);
    digitalWrite(M1_BACK_PIN, LOW);

  }
  else {
    //incorrect direction given
  }
}




void rst_enc_a_l_count() {
  enc_a_l_count = 0;
}

void rst_enc_b_l_count() {
  enc_b_l_count = 0;
}

void rst_enc_a_r_count() {
  enc_a_r_count = 0;
}

void rst_enc_b_r_count() {
  enc_a_l_count = 0;
}


void set_buzzer_on(){
  analogWrite(BUZZ_PIN, 2);
  //draws about 0.8ma
  //foroums say limit teensy pins to 1-4ma
}

void set_buzzer_off(){
  analogWrite(BUZZ_PIN, 0);
}

//no resistance, battery full charge
//160 measures about 6v
//150 measure about 6v
//140 measure about 5.9v

//reccomend 

//Ran with motor limit 140, 
//with motors maxed out, all emitters on, all leds on, (buzzer off), no resistance at wheels. it drew about 0.9A.



#define UPPER_MOTOR_LIMIT 140
#define LOWER_MOTOR_LIMIT 30
#define PID_POLLING_DELAY 15
#define MOTOR_SWITCH_DIR_DELAY 0

int last_spd;
void loop() {
  turn_all_emit_on();
  turn_all_led_on();
  analogWrite(BUZZ_PIN, 2);
  //0 == fwd, 1 = back 2 = stop
  //move forward for 2 seconds
  set_motor_l(0, UPPER_MOTOR_LIMIT);
  set_motor_r(0, UPPER_MOTOR_LIMIT);
  delay(5000);
  //stop motors briefly
  set_motor_l(2, 0);
  set_motor_r(2, 0);
  delay(MOTOR_SWITCH_DIR_DELAY);
  //move motors backwards for 2 seconds
  set_motor_l(1, UPPER_MOTOR_LIMIT);
  set_motor_r(1, UPPER_MOTOR_LIMIT);
  delay(5000);
  //stop motors briefly
  set_motor_l(2, 0);
  set_motor_l(2, 0);
  delay(MOTOR_SWITCH_DIR_DELAY);
  //turn left for 2 seconds
  set_motor_l(1, UPPER_MOTOR_LIMIT);
  set_motor_r(0, UPPER_MOTOR_LIMIT);
  delay(5000);
  //stop motors briefly
  set_motor_l(2, 0);
  set_motor_r(2, 0);
  delay(MOTOR_SWITCH_DIR_DELAY);
  //turn right for 2 seconds
  set_motor_l(0, UPPER_MOTOR_LIMIT);
  set_motor_r(1, UPPER_MOTOR_LIMIT);
  delay(5000);
  //stop motors briefly
  set_motor_l(2, 0);
  set_motor_r(2, 0);
  delay(MOTOR_SWITCH_DIR_DELAY);
  //Test incrementing/decrementing motor speeds
  //increment the motor speed from 0 to UPPER_MOTOR_LIMIT, then decrement it to 0
  turn_all_emit_off();
  turn_all_led_off();
  last_spd = 0;
  for (int i = 0; i < 5; i ++) { //repeat the sequence below 5 times
    //increment speed by 1
    for (last_spd = 0; last_spd < UPPER_MOTOR_LIMIT; last_spd++) {
      set_motor_l(0, last_spd);
      set_motor_r(0, last_spd);
      get_dist_r();
      get_dist_l();
      delay(PID_POLLING_DELAY);
    }
    //decrement speed by 1
    for (last_spd = UPPER_MOTOR_LIMIT; last_spd > 1; last_spd--) {
      set_motor_l(0, last_spd);
      set_motor_r(0, last_spd);
      get_dist_r();
      get_dist_l();
      delay(PID_POLLING_DELAY);
    }
    //increment speed by 3
    for (last_spd = 0; last_spd < UPPER_MOTOR_LIMIT; last_spd += 3) {
      set_motor_l(0, last_spd);
      set_motor_r(0, last_spd);
      get_dist_r();
      get_dist_l();
      delay(PID_POLLING_DELAY);
    }
    //decrement speed by 3
    for (last_spd = UPPER_MOTOR_LIMIT; last_spd > 1; last_spd -= 3) {
      set_motor_l(0, last_spd);
      set_motor_r(0, last_spd);
      get_dist_r();
      get_dist_l();
      delay(PID_POLLING_DELAY);
    }
    //increment speed by 7
    for (last_spd = 0; last_spd < UPPER_MOTOR_LIMIT; last_spd += 7) {
      set_motor_l(0, last_spd);
      set_motor_r(0, last_spd);
      get_dist_r();
      get_dist_l();
      delay(PID_POLLING_DELAY);
    }
    //decrement speed by 7
    for (last_spd = UPPER_MOTOR_LIMIT; last_spd > 1; last_spd -= 7) {
      set_motor_l(0, last_spd);
      set_motor_r(0, last_spd);
      get_dist_r();
      get_dist_l();
      delay(PID_POLLING_DELAY);
    }
    //increment speed by 15
    for (last_spd = 0; last_spd < UPPER_MOTOR_LIMIT; last_spd += 15) {
      set_motor_l(0, last_spd);
      set_motor_r(0, last_spd);
      get_dist_r();
      get_dist_l();
      delay(PID_POLLING_DELAY);
    }
    //decrement speed by 15
    for (last_spd = UPPER_MOTOR_LIMIT; last_spd > 1; last_spd -= 15) {
      set_motor_l(0, last_spd);
      set_motor_r(0, last_spd);
      get_dist_r();
      get_dist_l();
      delay(PID_POLLING_DELAY);
    }
  }

  set_motor_l(2, 0);
  set_motor_r(2, 0);

  //delay();

  //Serial.println(get_dist_l());

  //Serial.println(get_dist_r());
  //
  //    Serial.println(get_dist_fr());
  //
  //    Serial.println(get_dist_fl());
  //delay(100);
}

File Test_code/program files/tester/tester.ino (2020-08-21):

//IR Emitters (USE PHONE CAMERA)
//Recievers

typedef struct{
  int motorEN, motorForward, motorReverse;
} motor;

int thresh = 950;

motor TestMotor = {4,0,1}; //format as {motorEN,motorForward,motorReverse}
motor TestMotor1 = {5, 2, 3};

//MOTORS
//ENCODERS(a1, b1, a2, b2)
int led0 = 10;
int led1 = 11;
int buzz = 13;
int sw = 12;

int d0 = 22;
int d1 = 20;
int d2 = 15;
int d3 = 17;

int r0 = 23;
int r1 = 21;
int r2 = 14;
int r3 = 16;

int encoderA1 = 8;
int encoderB1 = 9;
int encoderA2 = 6;
int encoderB2 = 7;



void setup() {
  Serial.begin(9600);
  pinMode(led0, OUTPUT);
  pinMode(led1, OUTPUT);
  pinMode(buzz, OUTPUT);
  pinMode(sw, INPUT);
  
  //SET Emitter pins as OUTPUTS
  pinMode(d0, OUTPUT);
  pinMode(d1, OUTPUT);
  pinMode(d2, OUTPUT);
  pinMode(d3, OUTPUT);

  //SET Reciever pins as INPUTS
  pinMode(r0, INPUT);
  pinMode(r1, INPUT);
  pinMode(r2, INPUT);
  pinMode(r3, INPUT);
  //Set motor pins

  //set encoder pins

  //define interputs

}


void motor_seq(){
  // put your main code here, to run repeatedly:
  analogWrite(TestMotor.motorEN,80);
  analogWrite(TestMotor1.motorEN,80);
  // Run the motor forward for 2 seconds
  digitalWrite(TestMotor.motorForward,0);
  digitalWrite(TestMotor.motorReverse,1);

  digitalWrite(TestMotor1.motorForward,0);
  digitalWrite(TestMotor1.motorReverse,1);
//  
  delay(10);
//
//  // Run the motor backward for 2 seconds
//  digitalWrite(TestMotor1.motorForward,0);
//  digitalWrite(TestMotor1.motorReverse,1);
//  
//  digitalWrite(TestMotor.motorForward,0);
//  digitalWrite(TestMotor.motorReverse,1);
//  delay(2000);
}

void motor_stop(){
  analogWrite(TestMotor.motorEN,0);
  analogWrite(TestMotor1.motorEN,0);
  }

int dist(){
  int vall = 0;
  
  digitalWrite(22, HIGH);
  delay(10);
  vall = analogRead(23);
  delay(10);
  Serial.println(vall);
  digitalWrite(22, LOW);
  return vall;
}


void loop() {
  // put your main code here, to run repeatedly:
//  digitalWrite(led0, HIGH);
//  digitalWrite(led1, HIGH);
//  digitalWrite(buzz,HIGH);
//  Serial.println(digitalRead(sw));
//  delay(500);
//  digitalWrite(buzz,LOW);
//  delay(5000);
  motor_seq();
//  if(dist() >= thresh){motor_stop();}
//  else{motor_seq();}
  delay(100);
  
}

void ledState(int s)
{
}

void distance_test()
{
  
}
void motor_test()
{
  //
  
}
void encoder_test()
{
  
}

///Random//
//#include<random>
//Source of entropy "random devices"
//std::random_device device;

//Generate a psuedorandom sequence of bits --random engines
//std::default_random_engine engine{device()};

//Now just use the engine whenever I want random bits.


//Give me a distribution wehre I get values back from 1 to 6 inclusive with equal probaility
//std::uniform_int)distribution distribution{1,6};


//for (int i = 0; i < 1000; ++i)
//{
//  std::cout << distriution(engine)
//}

//
//
//////RAII
//////ACQUIRE Dynamic resources in contructors
//////We would want those construcors to fail(by thoriwng exception) if the acquisition failed
////
////
//////vector is an RAII array. 
////
////std::unique_ptr<A>a ;//when unique pointer dies, then it also deltes it with sus
////
////
////
////std::shared_ptr<>int p1{new int} // when last one dies, it deltes what it oints to
////
////ICS46_DYNAMIC)FACTORY_REGISTER(MazeGenerator, Lit Generator, "My Generator Is Lit")
////
////
////
//////override - this function overrides something in the base class
//
//std::vector<std::vector<int>> v(d1, std::vector<int> (d2,0));

//Swap values efficently


//template <typename T>
////void mySwap(T& t1, T& t2)
////{
////  T temp <== t1;
////  t1<==t2;
////  t2<==temp;
////  }
////C++
//
//int&& d = 3; //rvalue refrence
////r value refrence points to object hat is going to die anyways. 
//vector(vector&& v); //move constructor 
//
//vector<T>::vector(vector&& v)
//  : data{nullptr}, size{0}, capacity(0)
//  {
//    std::swap(data, v.data);
//    std::swap(size, v.size);
//    std::swap(capacity, v.capacity);
//    }
//
//
////STD move 
////Takes a value and gives you back an rvalue refrence to it
//// It lets you assume that something is about to die, even if it isn't.
//// 

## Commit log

2020-08-21 Board updates
2020-09-19 Kit-Mouse changes
    Current limiting R's on emitters
    Motors powered by battery
    Big caps on battery
    Debounce circuit on push switch
    [mouse_v2.sch]
2020-09-20 Final Schematic and PCB changes
    [_saved_mouse_v2.sch, mouse_v2.kicad_pcb, mouse_v2.sch]
2020-09-21 Updates
    PCB
    Foorprints
    [_saved_mouse_v2.sch, mouse_v2.sch]
2020-09-23 1uF Cap
    [mouse_v2.kicad_pcb, mouse_v2.sch]
2020-09-23 Silkscreen changes
    [mouse_v2.kicad_pcb]
2020-09-23 Final fixes
    [mouse_v2.kicad_pcb, mouse_v2.sch]
2020-09-23 Final Changes for real this time
    [mouse_v2.kicad_pcb]
2020-09-23 Final Fixes 3
    [mouse_v2.kicad_pcb]
2020-09-25 Pushing Plots
    [mouse_v2-B.Cu.gbr, mouse_v2-B.Mask.gbr, mouse_v2-B.Paste.gbr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]
2020-10-10 Updated Schematic Image
2020-10-10 Motor Image
2020-10-11 Added CAD Files
    [27 Rubber Band Wheel.SLDPRT, 27 Rubber Band Wheel.STL, Motor Offset.SLDPRT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]
2020-12-28 Add files via upload
    Updated Dimensions for 27 Rubber Band Wheel
    [27 Rubber Band Wheel.SLDPRT, 27 Rubber Band Wheel.STL]
2021-01-20 New Skate Design
    Smaller cross skate design
    [Mouse Skates.SLDPRT]
2021-01-30 Front Skates Added
    [flat skates.SLDPRT, flat skates.STL]
2021-02-13 started BLE adapter for rev1 of board
    [HC05_adapter.kicad_pcb, HC05_adapter.sch]
2021-03-31 started code for stress testing motors
2021-03-31 use unsigned int for motor counts
2021-03-31 modify PWM frequency
2021-04-10 create arduino version
2021-04-19 tested total current draw(w/o buzzer)
    [stress_test_arduino.ino]
2021-04-26 Daughter Board
    Basic Daughter Board for the HC-05
    [V1 Daughter Board.kicad_pcb, V1 Daughter Board.sch, mouse_v2.kicad_pcb]
